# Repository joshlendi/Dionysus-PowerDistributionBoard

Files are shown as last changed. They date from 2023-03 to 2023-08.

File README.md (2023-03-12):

# Dionysus: Automated Indoor Hydroponic Garden

## Description
The NFT hydroponic garden will consist of four vertical rows with five plants each. The structure will contain all necessary systems to grow small plants. 
The control system will be a closed-loop model based design deployed to an Arduino Due. An optional nutrient control system will monitor and adjust plant nutrient levels during operation. 

## Table of Contents
* Installation
* Contributing
* Credits
* License

## Installation
1. Download [Dionysus-Power Distribution Board] and unzip
2. Open the KiCAD project folder. **Note**, some symbols' and footprints' may need correction. All symbols and footprints can be found in the *libraries* folder within the project.

## Contributing
* See [CONTRIBUTING.md](https://github.com/joshlendi/Dionysus-PowerDistributionBoard/blob/master/CONTRIBUTING) for more information

## Credits
* Include a section for credits in order to highlight and link to the authors of your project.

## License
* GNU General Public License v3.0
	* See [LICENSE.md](https://github.com/joshlendi/Dionysus-PowerDistributionBoard/blob/master/LICENSE) for more information

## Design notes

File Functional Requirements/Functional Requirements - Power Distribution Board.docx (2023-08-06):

# Dionysus Power Distribution Board

# Functional Requirements [XX/XX/XXXX]

Contents

# Overview

The overview section should include a brief description of the project and functionality so that someone outside of the project team would be able to understand the project. The section should include a list of commonly used acronyms and abbreviations, a list of system components and their purpose, and inputs and outputs as discussed on the I/O list deliverable.

## Description

The Dionysus project will be a self-sufficient NFT hydroponic garden capable of growing small vegetables and herbs. The controller for Dionysus will be an Arduino Due microcontroller embedded in the power distribution motherboard.

The purpose is to create a control board that can handle the inputs and outputs necessary to operate a Dionysus system. Today’s microcontrollers and single board computers are not capable of driving all the components required. Additional hardware and circuitry are required.

Rather than a larger collection of harnessing, piggyback boards, and modifications, a single power distribution board will be created to handle the necessary inputs, outputs, and communications.

## Scope

In Scope | Out of Scope
Self-contained computer power | Raspberry Pi Model 4 and Compute Module compatibility
GPIO for IO expansion | Voltage and current feedback measurements on input/outputs
Raspberry Pi or Arduino based microcontroller | True grow light drivers
E-stop circuitry
Ability to add an optional nutrient control system

## Acronyms and Abbreviations

Acronym | Meaning | Notes
NCS | Nutrient Control System | XXXXXXXXXXX
LED | Light-emitting Diode | XXXXXXXXXXX
TWI | Two-Wire Interface | Also known as I2C
TWD | Two-Wire Data | Also known as SDA
TWCK | Two-Wire Clock | Also known as SCL
CAN | Controller Area Network
USART | Universal Asynchronous Receive/Transmit
SPI | Serial Peripheral Interface
STB | Short to Battery
STG | Short to Ground

# System Components

Abbreviation | Meaning | Notes
XXXXX | XXXXXXXXX | XXXXXXXXXXXXXX

# Board Controller

The system controller will be an Arduino Due powered by a 32-bit ARM Cortex-M3 processor. The board contains 54 digital input/output pins, 12 analog inputs, and 2 digital-to-analog pins. For communication, it has 4 UART busses, 2 TWI, and a single SPI header. Refer to Arduino’s official website (https://store-usa.arduino.cc/products/arduino-due?selectedStore=us) for more information.

The Due board will be installed as a piggy back board using stacking header pins. This does require an Arduino Due without headers to be purchased and have stacked headers added. Power will be provided to the power input pin through these headers.

The Due board operates at 3.3V. Therefore, all logical inputs and outputs will be restricted to 3.3V, and communications are restricted to 3.3V logic levels.

Board Specifications

Microcontroller: AT91SAM3X8E

Operating Voltage: 3.3 VDC

Input Voltage: 6-16 VDC (7-12 VDC recommended)

Digital I/O Pins: 54

Analog Input Pins: 12

Analog Output Pins: 2

I/O Output Current Total: 130 mA

3.3V Power Pin Current: 800 mA

5V Power Pin Current: 800 mA

Flash Memory: 512 KB

SRAM: 96KB

Clock Speed: 84 Mhz

# Inputs

Name | Description
Ambient Temperature | Ambient temperature of environment
Ambient Light | Ambient light available to plants
Emergency Stop Feedback | Emergency stop feedback to control system
NCS Flow Rate | Volumetric flow rate going through nutrient control system
NCS Temperature In | Input temperature to nutrient control system
Chemical 1 Level Minimum | Chemical 1 tank almost empty. Signals operator to refill tank.
Chemical 2 Level Minimum | Chemical 2 tank almost empty. Signals operator to refill tank.
Chemical 3 Level Minimum | Chemical 3 tank almost empty. Signals operator to refill tank.
Chemical 4 Level Minimum | Chemical 4 tank almost empty. Signals operator to refill tank.
Chemical 5 Level Minimum | Chemical 5 tank almost empty. Signals operator to refill tank.
Chemical 1 Pump Feedback | Chemical 1 peristaltic pump dispensing active
Chemical 2 Pump Feedback | Chemical 2 peristaltic pump dispensing active
Chemical 3 Pump Feedback | Chemical 3 peristaltic pump dispensing active
Chemical 4 Pump Feedback | Chemical 4 peristaltic pump dispensing active
Chemical 5 Pump Feedback | Chemical 5 peristaltic pump dispensing active
Reservoir pH | Reservoir pH level measured in nutrient control system
Reservoir Flow Rate | Volumetric flow rate out of reservoir
Reservoir Temperature In | Input temperature to reservoir
Reservoir Temperature Out | Output temperature of reservoir
Reservoir TDS | Reservoir total dissolved solids measured in nutrient control system
Reservoir Level Minimum | Reservoir water level almost empty

## Input Processing

The input processing section should include a description of the input processing requirements of the system. This should cover details about Debounce, Anti Tie-down, Overrides, dead banding, and other project specific input processing options.

# Outputs

Name | Abbreviation | Description
LED Channel 1 | LEDCh1 | 3-wire RGB LED channel 1
LED Channel 2 | LEDCh2 | 3-wire RGB LED channel 2
LED Channel 3 | LEDCh3 | 3-wire RGB LED channel 3
LED Channel 4 | LEDCh4 | 3-wire RGB LED channel 4
LED Channel 5 | LEDCh5 | 3-wire RGB LED channel 5
LED Channel 6 | LEDCh6 | 3-wire RGB LED channel 6
LED Channel 7 | LEDCh7 | 3-wire RGB LED channel 7
LED Channel 8 | LEDCh8 | 3-wire RGB LED channel 8
NCS Pump Activation | NCSPmpAct | Nutrient control system water pump activation
Reservoir Heater Activation | RsvrHeaterAct | Reservoir heater activation
Reservoir Pump Activation | RsvrPmpAct | Reservoir water pump activation
Chemical 1 Pump | Chem1Pmp | Chemical 1 peristaltic dispensing control
Chemical 2 Pump | Chem2Pmp | Chemical 2 peristaltic dispensing control
Chemical 3 Pump | Chem3Pmp | Chemical 3 peristaltic dispensing control
Chemical 4 Pump | Chem4Pmp | Chemical 4 peristaltic dispensing control
Chemical 5 Pump | Chem5Pmp | Chemical 5 peristaltic dispensing control

## Output Processing

This section should be used if there are outputs to be processed by the control system.

# Power Management Controller

The Arduino Due board requires 7 VDC to 12 VDC. The water pump(s) and reservoir heater activation use a FET to provide medium to high power to AC relays. Flyback protection should be used. The chemical peristaltic pumps and grow lights operate between 12 and 24 volts.

Power regulation is required for the board. Power management will consist of voltage regulation for the board’s controller, sensors, and other low power accessories. Four high side drivers will be used to power larger loads, such as peristaltic pumps, grow lights, and water pump relay coil activation.

The board must have an input voltage of 12 to 24 volts DC. Circuit protections must be used to protect the board from reverse polarity, overvoltage, and overcurrent.

The board must output voltages at 3.3 VDC, 9 VDC, and input voltage ranges. Each power source shall be protected by circuit protection devices. Fuses should be used for each device powered and located as close to the source as possible.

[need to specify what devices are powered by which bus]

[insert the power management calculation tables here]

[Specify the current limits for each power rail]

# Subsystems

## Two-Wire Interface Bus Isolator

The Atlas Scientific EZO boards require voltage isolation if multiple boards are used on the same two-wire bus. Each EZO board will have a voltage and communication isolator circuit. It uses a two-wire interface digital isolator along with an isolated DC-DC converter.

The isolated busses require termination resistors.

## GPIO

10 digital input/outputs and 5 analog inputs are available as general purpose input/outputs. These are available to the end user for additional sensors and system input/outputs.

Digital input/outputs should be protected against short to battery and short to ground

Overvoltage protection, overcurrent protection, back EMF protection, current limiting, basic filtering, external clipping diodes

## Pulse Width Modulation Controller

The grow lights used will be 3-wire RGB LED lights requiring brightness and color control. An RGB PWM LED driver will be used to drive at least 2 channels of grow lights. Additional channels may be add if space and circuitry constraints allow. Red and blue will be the main colors used.

PWM control will be used to control the brightness of the LEDs. This simulates the rising and setting of the sun.

Optional feature would be a way to create sectors of addressable LEDs. This would allow for simulating the sun moving east to west in the sky.

## Real-time Clock

This optional feature would be nice to have for data logging and future product improvements.

## Temperature Sensor

For the first design iteration, digital 1-wire temperature sensors, Maxim DS18B20, are acceptable. They require no additional hardware or circuitry to integrate. The digital communication bus must be scanned on start up to search for all available sensors.

5 temperature sensor channels are available.

There is no requirement for PCBA temperature sensors. The circuit board should have at least 1 temperature sensor installed for board diagnostics and ambient redundancy.

## CAN Bus

The microcontroller has CAN bus communication available. A CAN bus transceiver will be implemented into the PDB. CAN high and low will be externally available to the end user for additional functionality.

CAN high, low, 12 volt power, and 12 volt ground will be available in a four pin terminal block.

The CAN bus has selectable termination using a selector switch.

## EZO Board

The motherboard will allow for at least 4 Atlas Scientific EZO sensor boards. They use 2-three pin headers in a daughterboard configuration. Any EZO board must be compatible in any of the four spots.

A BNC or three pin terminal block will be used to connect the EZO sensor to the power distribution board.

## Peristaltic Pump

The Atlas Scientific peristaltic pumps will be used. These require 12 to 24 volt power for the motor and 3.3 to 5 volt power for the control section. Motor power is supplied through a two pin terminal block on the PDB and pump. The control section uses a Molex connection.

The circuit board must accommodate at least 5 peristaltic pumps.

## Water Pump

The PDB must be able to drive 2 AC relays. These will activate the reservoir and nutrient control system pumps. Each pump output will have its own two position terminal block, a positive and negative.

## Water Heater

The PDB must be able to drive an AC relay that provides power to the reservoir heater.

## Air Pump

The PDB must be able to drive an AC relay that provides power to the reservoir air pump.

# Operating Mode

This section should define conditional operating modes of the system for expected use.

# Failure Modes

A failure mode is a mode that the system may enter into automatically upon a system fault. The most common system faults occur at an input or an output. This section should list potential input/output/communication faults and system responses.

# Communications

This section should describe the modes of communication used on the project, examples including CAN, Radio, Ethernet, Multiplex, etc.

The circuit board will be a flexible design for the end user. Some or all of the inputs, outputs, and sensors may be used. Internal communication must be flexible. A two-wire interface bus will be used for internal board communication. The EC, pH, flow meter, and peristaltic pumps specified for this project are TWI and UART compatible. UART is simpler in its design but does not allow for the flexibility that a TWI bus has.

All communication busses will have selectable termination resistors at various points to allow the end user to select where the bus is terminated.

An external connector will be provided for TWI communication to an external board should once be added.

# Limiting and Interlock

This section should describe the components/devices/functionality which will limit functionality or provide interlock signals for the device. This section should describe what components allow for expected functional use.

## Emergency Stop Device Interlock

The emergency stop device interlock consists of two circuits: a hardwired loop and feedback signal.

The feedback signal provides confirmation to the control system to prevent false errors.

The hardwired loop runs through various connectors to prevent power from being delivered to various components.

# Calibrations

This section should list the expected calibrated inputs to the system.

# Diagnostics

This section should list the planned diagnostic/health information that is intended.

## LED Indication

LED indication will be provided for all major functions of the board.

Indication Color | Function
Green | Device functioning properly
Yellow | Device functionality limited, but not crucial to operation
Red | Device error occurred. Functionality is disabled.
Blue
Orange/Amber

Indication Pattern | Function
Solid
Flashing
Flashing

Component | Component Signal | Color
Input Voltage | - | Green
3.3V Regulator | Regulator output | Green
5.0V Regulator | Regulator output | Green
High Side Drivers | Driver output | Green
Chemical Pumps | Pump interrupt | Green
NCS Pump | Pump FET activation | Green
Reservoir Pump | Pump FET activation | Green
Reservoir Heater | Heater FET activation | Green
TWI Busses | Data FET | Green
UART Bus | Data FET | Green
CAN Bus | Data FET | Green

# External Connect

Header pins are available for all communication busses.

# Telematics

This board does not contain any ability to transmit data.

# Data Logging

This board does not contain any ability to log data.

# Applicable Standards

This section should list the standard requirements for the project, as well as the expected use of standardized information, such as EPS, Library Blocks, IEEE, SAE, etc.

# Appendix

# Figures

# Tables

# Revision History

Revision History
When: | Who: | What:
XX/XX/XXXX | XXXXXXX | XXXXXXXXXXXXXXXXXXXXXXXXX

Functional Requirement

DocXXXXXXX XX/XX/XXXX

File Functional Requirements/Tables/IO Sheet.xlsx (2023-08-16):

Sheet: IO Statistics
 | Power | 12
 | Ground | 9
Inputs | Keyswitch | #REF!
 | Switch-to-Battery | #REF!
 | Switch-to-Ground | #REF!
 | Voltage-to-Digital | #REF!
Outputs | Switch-to-Battery | #REF!
 | Switch-to-Ground | #REF!
 | Pulse Width Modulation | #REF!
Communication | Two Wire Interface | #REF!

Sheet: IO Sheet
Signal Name | Description | Direction | Type | Point A |  |  | Point B
 |  |  |  | Device 1 | Device 1 Connector | Pin | Device 2 | Device 2 Connector | Pin
Vin | Input power | Power | PWR | Internal - PMC | - | - | Power | TB1 | 1
Ground |  | Power | GND | Internal - PMC | - | - | Power | TB1 | 2
Keyswitch |  | Input | KEYSW | Internal - PMC | - | - | System | TB2 | 1
EStopDevOut | Estop loop power - start of loop | Power | PWR | Internal - Sys | - | - | System | TB2 | 2
EStopDevIn | Estop loop - end of loop | Input | STB | Arduino Due | Controller header | D24 | System | TB2 | 3
EStopFdbk | Emergency stop feedback | Input | STB | Arduino Due | Controller header | D25 | System | TB2 | 4
CtrlReset | Microcontroller Reset | Input | STG | Arduino Due | Controller header | RESET | System | TB2 | 5
AmbLit | Ambient light sensor | Input | VTD | Arduino Due | Controller header | A9 | Sensor | TB3 | 1
RsvrLvlMin | Reservoir level minimum | Input | STB | Arduino Due | Controller header | D35 | Sensor | TB3 | 2
AmbTemp | Ambient temperature sensor | Comm | 1-Wire | Arduino Due | Controller header | D35 | Sensor | TB3 | 3
RsvrTempIn | Reservoir temperature in | Comm | 1-Wire | Arduino Due | Controller header | D35 | Sensor | TB3 | 4
RsvrTempOut | Reservoir temperature out | Comm | 1-Wire | Arduino Due | Controller header | D35 | Sensor | TB3 | 5
SpareTemp | Spare temperature sensor | Comm | 1-Wire | Arduino Due | Controller header | D35 | Sensor | TB3 | 6
AmbEnv - TWCK | Ambient environment sensor | Comm | TWCK | Arduino Due | Controller header | SCL | Sensor | TB3 | 7
AmbEnv - TWD | Ambient environment sensor | Comm | TWD | Arduino Due | Controller header | SDA | Sensor | TB3 | 8
AccPwr1 | 3.3V accessory power | Power | PWR | Internal - PMC | - | - | Sensor | TB3 | 9
Ground |  | Power | GND | Internal - PMC | - | - | Sensor | TB3 | 10
MainPwr1 | Reservoir pump power | Power | PWR | Internal - PMC | - | - | Reservoir Pump | TB4 | 1
Ground |  | Power | GND | Internal - PMC | - | - | Reservoir Pump | TB4 | 2
MainPwr2 | Reservoir heater power | Power | PWR | Internal - PMC | - | - | Reservoir Heater | TB5 | 1
Ground |  | Power | GND | Internal - PMC | - | - | Reservoir Heater | TB5 | 2
Nutr1LvlMin | Nutrient 1 Level Minimum | Input | STB | Arduino Due | Controller header | D44 | NCS | TB6 | 1
Nutr1PerPmpInt | Nutrient 1 Peristalic Pump Interrupt | Input | STB | Arduino Due | Controller header | D45 | NCS | TB6 | 2
Nutr2LvlMin | Nutrient 2 Level Minimum | Input | STB | Arduino Due | Controller header | D46 | NCS | TB6 | 3
Nutr2PerPmpInt | Nutrient 2 Peristalic Pump Interrupt | Input | STB | Arduino Due | Controller header | D47 | NCS | TB6 | 4
Nutr3LvlMin | Nutrient 3 Level Minimum | Input | STB | Arduino Due | Controller header | D48 | NCS | TB6 | 5
Nutr3PerPmpInt | Nutrient 3 Peristalic Pump Interrupt | Input | STB | Arduino Due | Controller header | D49 | NCS | TB6 | 6
PhDecrLvlMin | pH Decrease Level Minimum | Input | STB | Arduino Due | Controller header | D50 | NCS | TB6 | 7
PhDecrPerPmpInt | pH Decrease Peristalic Pump Interrupt | Input | STB | Arduino Due | Controller header | D51 | NCS | TB6 | 8
PhIncrLvlMin | pH Increase Level Minimum | Input | STB | Arduino Due | Controller header | D52 | NCS | TB6 | 9
PhIncrPerPmpInt | pH Increase Peristalic Pump Interrupt | Input | STB | Arduino Due | Controller header | D53 | NCS | TB6 | 10
NCSTempIn | Nutrient Control System Temperature In | Comm | 1-Wire | Arduino Due | Controller header | D35 | NCS | TB6 | 11
NCS - TWCK | Nutrient Control System TWI bus | Comm | TWCK | Arduino Due | Controller header | SCL | NCS | TB6 | 12
NCS - TWD | Nutrient Control System TWI bus | Comm | TWD | Arduino Due | Controller header | SDA | NCS | TB6 | 13
AccPwr3 | 3.3V accessory power | Power | PWR | Internal - PMC | - | - | NCS | TB6 | 14
Ground |  | Power | GND | Internal - PMC | - | - | NCS | TB6 | 15
MainPwr4 | NCS pump power | Power | PWR | Internal - PMC | - | - | NCS Pump | TB7 | 1
Ground |  | Power | GND | Internal - PMC | - | - | NCS Pump | TB7 | 2
D1 | General purpose input/output pins |  |  | Arduino Due | Controller header | D2 | GPIO - Digital | TB8 | 1
D2 | General purpose input/output pins |  |  | Arduino Due | Controller header | D3 | GPIO - Digital | TB8 | 2
D3 | General purpose input/output pins |  |  | Arduino Due | Controller header | D4 | GPIO - Digital | TB8 | 3
D4 | General purpose input/output pins |  |  | Arduino Due | Controller header | D5 | GPIO - Digital | TB8 | 4
D5 | General purpose input/output pins |  |  | Arduino Due | Controller header | D6 | GPIO - Digital | TB8 | 5
D6 | General purpose input/output pins |  |  | Arduino Due | Controller header | D7 | GPIO - Digital | TB8 | 6
D7 | General purpose input/output pins |  |  | Arduino Due | Controller header | D8 | GPIO - Digital | TB8 | 7
D8 | General purpose input/output pins |  |  | Arduino Due | Controller header | D9 | GPIO - Digital | TB8 | 8
D9 | General purpose input/output pins |  |  | Arduino Due | Controller header | D10 | GPIO - Digital | TB8 | 9
D10 | General purpose input/output pins |  |  | Arduino Due | Controller header | D11 | GPIO - Digital | TB8 | 10
AccPwr2 | 3.3V accessory power | Power | PWR | Internal - PMC | - | - | GPIO - Digital | TB8 | 11
Ground |  | Power | GND | Internal - PMC | - | - | GPIO - Digital | TB8 | 12
A1 | General purpose analog input pins | Input | VTD | Arduino Due | Controller header | A0 | GPIO - Analog | TB9 | 1
A2 | General purpose analog input pins | Input | VTD | Arduino Due | Controller header | A1 | GPIO - Analog | TB9 | 2
A3 | General purpose analog input pins | Input | VTD | Arduino Due | Controller header | A2 | GPIO - Analog | TB9 | 3
A4 | General purpose analog input pins | Input | VTD | Arduino Due | Controller header | A3 | GPIO - Analog | TB9 | 4
A5 | General purpose analog input pins | Input | VTD | Arduino Due | Controller header | A4 | GPIO - Analog | TB9 | 5
DAC1 | General purpose analog output pins | Output | VTD | Arduino Due | Controller header | DAC1 | GPIO - Analog | TB9 | 6
DAC2 | General purpose analog output pins | Output | VTD | Arduino Due | Controller header | DAC2 | GPIO - Analog | TB9 | 7
AccPwr2 | 3.3V accessory power | Power | PWR | Internal - PMC | - | - | GPIO - Analog | TB9 | 8
Ground |  | Power | GND | Internal - PMC | - | - | GPIO - Analog | TB9 | 9
TWCK0 | Two-wire interface bus 1 | Comm | TWCK | Arduino Due | Controller header | D21/SCL | GPIO - Comm | TB10 | 1
TWD0 | Two-wire interface bus 1 | Comm | TWD | Arduino Due | Controller header | D20/SDA | GPIO - Comm | TB10 | 2
TWCK1 | Two-wire interface bus 2 | Comm | TWCK | Arduino Due | Controller header | SCL1 | GPIO - Comm | TB10 | 3
TWD1 | Two-wire interface bus 2 | Comm | TWD | Arduino Due | Controller header | SDA1 | GPIO - Comm | TB10 | 4
RXD | USART bus receive | Comm | USART | Arduino Due | Controller header | D0/RX0 | GPIO - Comm | TB10 | 5
TXD | USART bus transmit | Comm | USART | Arduino Due | Controller header | D1/TX0 | GPIO - Comm | TB10 | 6
CAN-H | CAN bus 1 | Comm | CAN-H | Internal - GPIO | - | - | GPIO - Comm | TB10 | 7
CAN-L | CAN bus 1 | Comm | CAN-L | Internal - GPIO | - | - | GPIO - Comm | TB10 | 8
1-Wire | 1-Wire header | Comm | 1-Wire | Arduino Due | Controller header | D35 | GPIO - Comm | TB10 | 9
AccPwr2 | 3.3V accessory power | Power | PWR | Internal - PMC | - | - | GPIO - Comm | TB10 | 10
Ground |  | Power | GND | Internal - PMC | - | - | GPIO - Comm | TB10 | 11
LEDCh1-R | LED Channel 1 - Red | Output | PWM | Internal - LED Ctrl | - | - | LED Ch1 | TB11 | 1
LEDCh1-G | LED Channel 1 - Green | Output | PWM | Internal - LED Ctrl | - | - | LED Ch1 | TB11 | 2
LEDCh1-B | LED Channel 1 - Blue | Output | PWM | Internal - LED Ctrl | - | - | LED Ch1 | TB11 | 3
LEDCh2-R | LED Channel 2 - Red | Output | PWM | Internal - LED Ctrl | - | - | LED Ch2 | TB12 | 1
LEDCh2-G | LED Channel 2 - Green | Output | PWM | Internal - LED Ctrl | - | - | LED Ch2 | TB12 | 2
LEDCh2-B | LED Channel 2 - Blue | Output | PWM | Internal - LED Ctrl | - | - | LED Ch2 | TB12 | 3
LEDCh3 - R | LED Channel 3 - Red | Output | PWM | Internal - LED Ctrl | - | - | LED Ch3 | TB13 | 1
LEDCh3 - G | LED Channel 3 - Green | Output | PWM | Internal - LED Ctrl | - | - | LED Ch3 | TB13 | 2
LEDCh3 - B | LED Channel 3 - Blue | Output | PWM | Internal - LED Ctrl | - | - | LED Ch3 | TB13 | 3
LEDCh4 -R | LED Channel 4 -Red | Output | PWM | Internal - LED Ctrl | - | - | LED Ch4 | TB14 | 1
LEDCh4 -G | LED Channel 4 -Green | Output | PWM | Internal - LED Ctrl | - | - | LED Ch4 | TB14 | 2
LEDCh4 -B | LED Channel 4 -Blue | Output | PWM | Internal - LED Ctrl | - | - | LED Ch4 | TB14 | 3
LEDCh5 -R | LED Channel 5 -Red | Output | PWM | Internal - LED Ctrl | - | - | LED Ch5 | TB15 | 1
LEDCh5 -G | LED Channel 5 -Green | Output | PWM | Internal - LED Ctrl | - | - | LED Ch5 | TB15 | 2
LEDCh5 -B | LED Channel 5 -Blue | Output | PWM | Internal - LED Ctrl | - | - | LED Ch5 | TB15 | 3
LEDCh6 -R | LED Channel 6 -Red | Output | PWM | Internal - LED Ctrl | - | - | LED Ch6 | TB16 | 1
LEDCh6 -G | LED Channel 6 -Green | Output | PWM | Internal - LED Ctrl | - | - | LED Ch6 | TB16 | 2
LEDCh6 -B | LED Channel 6 -Blue | Output | PWM | Internal - LED Ctrl | - | - | LED Ch6 | TB16 | 3
LEDCh7 - R | LED Channel 7 - Red | Output | PWM | Internal - LED Ctrl | - | - | LED Ch7 | TB17 | 1
LEDCh7 - G | LED Channel 7 - Green | Output | PWM | Internal - LED Ctrl | - | - | LED Ch7 | TB17 | 2
LEDCh7 - B | LED Channel 7 - Blue | Output | PWM | Internal - LED Ctrl | - | - | LED Ch7 | TB17 | 3
LEDCh8 - R | LED Channel 8 - Red | Output | PWM | Internal - LED Ctrl | - | - | LED Ch8 | TB18 | 1
LEDCh8 - G | LED Channel 8 - Green | Output | PWM | Internal - LED Ctrl | - | - | LED Ch8 | TB18 | 2
LEDCh8 - B | LED Channel 8 - Blue | Output | PWM | Internal - LED Ctrl | - | - | LED Ch8 | TB18 | 3
CtrlPwr | 9V controller power | Power | PWR | Internal - PMC | - | - | Arduino Due | Controller header | VIN
MainPwr3 | Grow light power | Power | PWR | Internal - PMC | - | - | Internal - LED Ctrl | - | -
TWCK | LED Driver 1 TWI Bus | Comm | TWCK | Arduino Due | Controller header
TWD | LED Driver 1 TWI Bus | Comm | TWD | Arduino Due | Controller header
TWCK | LED Driver 2 TWI Bus | Comm | TWCK | Arduino Due | Controller header
TWD | LED Driver 2 TWI Bus | Comm | TWD | Arduino Due | Controller header
NCSPmpAct | Nutrient Control System Pump Activation | Output | STB | Arduino Due | Controller header | D42
NCSPmpActFdbk | Nutrient Control System Pump Activation Feedback | Input | STB | Arduino Due | Controller header | D43
AccPwrAct | Accessory power activation | Output | STB | Arduino Due | Controller header | D22
MainPwrAct | Main power activation | Output | STB | Arduino Due | Controller header | D23
MainPwr1Fdbk | Main power 1 measured feedback current | Input | VTD | Arduino Due | Controller header | A5
MainPwr2Fdbk | Main power 2 measured feedback current | Input | VTD | Arduino Due | Controller header | A6
MainPwr3Fdbk | Main power 3 measured feedback current | Input | VTD | Arduino Due | Controller header | A7
MainPwr4Fdbk | Main power 4 measured feedback current | Input | VTD | Arduino Due | Controller header | A8
RsvrPmpAct | Reservoir pump activation | Output | STB | Arduino Due | Controller header | D26
RsvrPmpActFdbk | Reservoir pump activation feedback | Input | STB | Arduino Due | Controller header | D27
RsvrHeaterAct | Reservoir heater activation | Output | STB | Arduino Due | Controller header | D28
RsvrHeaterActFdbk | Reservoir heater activation feedback | Input | STB | Arduino Due | Controller header | D29
CANRX | CAN bus | Comm | CAN | Arduino Due | Controller header | CANRX | Internal - GPIO
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

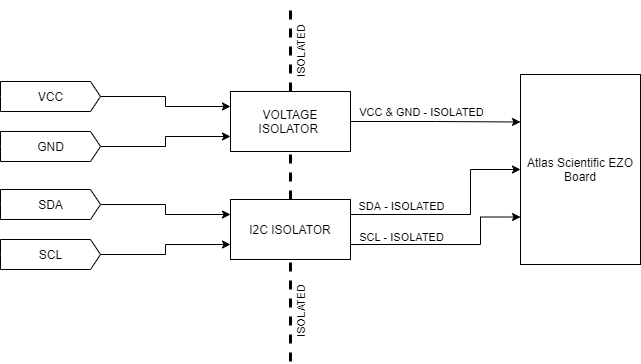
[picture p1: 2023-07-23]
Functional Requirements/Figures/Functional Requirements - Power Distribution Board_Diagrams-I2C Bus Isolator.png

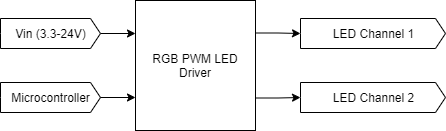
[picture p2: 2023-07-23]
Functional Requirements/Figures/Functional Requirements - Power Distribution Board_Diagrams-PWM.png

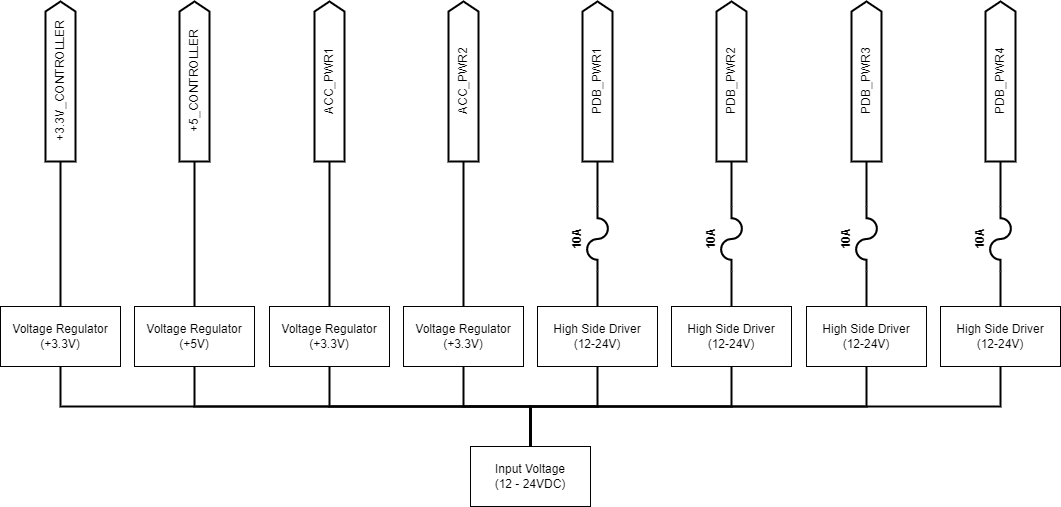
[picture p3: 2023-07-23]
Functional Requirements/Figures/Functional Requirements - Power Distribution Board_Diagrams-Power Management.png

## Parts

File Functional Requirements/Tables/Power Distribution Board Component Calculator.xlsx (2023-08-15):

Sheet: Total Power Requirements
 | Input Voltage [V] | Input Current [A] | Input Power [W] | Efficiency [%] | Output Voltage [V] | Current [A] | Power [W]
Accessory Power 1 | 12.00 | 1.16 | 13.89 | 95% | 3.30 | 4.00 | 13.20
Accessory Power 2 | 12.00 | 0.18 | 2.11 | 95% | 3.30 | 0.61 | 2.00
Accessory Power 3 | 12.00 | 0.39 | 4.71 | 95% | 3.30 | 1.35 | 4.47
Controller Power 1 | 12.00 | 0.79 | 9.47 | 95% | 9.00 | 1.00 | 9.00
Main Power 1 | 12.00 | 1.05 | 12.63 | 95% | 12.00 | 1.00 | 12.00
Main Power 2 | 12.00 | 1.05 | 12.63 | 95% | 12.00 | 1.00 | 12.00
Main Power 3 | 12.00 | 1.05 | 12.63 | 95% | 12.00 | 1.00 | 12.00
Main Power 4 | 12.00 | 2.11 | 25.26 | 95% | 12.00 | 2.00 | 24.00
Total | 12.00 | 7.78 | 93.34
Table #: Total Bus Power Requirements
 | Input Voltage [V] | Input Current [A] | Input Power [W] | Efficiency [%] | Output Voltage [V] | Current [A] | Power [W]
Accessory Power 1 | 12.00 | 0.00 | 0.00 | 95% | 3.30 |  | 0.00
Accessory Power 2 | 12.00 | 0.00 | 0.00 | 95% | 3.30 |  | 0.00
Accessory Power 3 | 12.00 | 0.00 | 0.00 | 95% | 3.30 |  | 0.00
Controller Power 1 | 12.00 | 0.00 | 0.00 | 95% | 9.00 |  | 0.00
Main Power 1 | 12.00 | 0.00 | 0.00 | 95% | 12.00 |  | 0.00
Main Power 2 | 12.00 | 0.00 | 0.00 | 95% | 12.00 |  | 0.00
Main Power 3 | 12.00 | 0.00 | 0.00 | 95% | 12.00 |  | 0.00
Main Power 4 | 12.00 | 0.00 | 0.00 | 95% | 12.00 |  | 0.00
Total | 12.00 | 0.00 | 0.00
Table #: Bus Power Limits

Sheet: Accessory Power Bus - 3.3V
Device | Qty | Voltage [V] | Current [A] | Power [W] | Total Current [A] | Total Power [W]
GPIO Header | 15 | 3.30 | 0.20 | 0.66 | 3.00 | 9.90
Communication Headers | 5 | 3.30 | 0.20 | 0.66 | 1.00 | 3.30
 |  |  |  |  | 4.00 | 13.20
Table #: Accessory Power 2 - 3.3V Devices
Device | Qty | Voltage [V] | Current [A] | Power [W] | Total Current [A] | Total Power [W]
Liquid Level Switch | 3 | 3.30 | 0.0025 | 0.01 | 0.01 | 0.02
Temperature Sensor | 5 | 3.30 | 0.10 | 0.33 | 0.50 | 1.65
Ambient Environment Sensor | 1 | 3.30 | 0.10 | 0.33 | 0.10 | 0.33
 |  |  |  |  | 0.61 | 2.00
Table #: Accessory Power 1 - 3.3V Devices
Device | Qty | Voltage [V] | Current [A] | Power [W] | Total Current [A] | Total Power [W]
Peristaltic Pump Logic | 5 | 3.30 | 0.01 | 0.04 | 0.06 | 0.21
Liquid Level Switch | 5 | 3.30 | 0.0025 | 0.01 | 0.01 | 0.04
Isolated DC-DC converter | 4 | 3.30 | 0.20 | 0.66 | 0.80 | 2.64
Digital TWI Isolator | 4 | 3.30 | 0.12 | 0.40 | 0.48 | 1.58
 |  |  |  | 0.00 | 0.00 | 0.00
 |  |  |  |  | 1.29 | 4.27
Table #: Accessory Power 3 - 3.3V Devices
Device | Qty | Voltage [V] | Current [A] | Power [W] | Total Current [A] | Total Power [W]
Accessory Power 1 |  | 3.30 | 0.0025 | 0.01 | 0.01 | 0.02
Accessory Power 2 |  | 3.30 | 0.10 | 0.33 | 0.50 | 1.65
Accessory Power 3 |  | 3.30 | 0.10 | 0.33 | 0.10 | 0.33
 |  |  |  |  | 0.61 | 2.00
Table #: Accessory Power Bus - 3.3V Total

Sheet: Controller Power Bus - 9V
Device | Qty | Voltage [V] | Current [A] | Power [W] | Total Current [A] | Total Power [W]
Arduino Due Controller | 1 | 9.00 | 1.00 | 9.00 | 1.00 | 9.00
 |  |  |  |  | 1.00 | 9.00
Table #:
Device | Qty | Voltage [V] | Current [A] | Power [W] | Total Current [A] | Total Power [W]
 |  |  |  |  | 0.00 | 0.00
Table #:
Device | Qty | Voltage [V] | Current [A] | Power [W] | Total Current [A] | Total Power [W]
 |  |  |  |  | 0.00 | 0.00
Table #:

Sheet: Main Power Bus - Vin
Device | Qty | Voltage [V] | Current [A] | Power [W] | Total Current [A] | Total Power [W]
Reservoir Pump Activation | 1 | 12.00 | 1.00 | 12.00 | 1.00 | 12.00
 |  |  |  |  | 1.00 | 12.00
Table #: Main Power 1 - Vin Devices
Device | Qty | Voltage [V] | Current [A] | Power [W] | Total Current [A] | Total Power [W]
Reservoir Heater Activation | 1 | 12.00 | 1.00 | 12.00 | 1.00 | 12.00
 |  |  |  |  | 1.00 | 12.00
Table #: Main Power 2 - Vin Devices
Device | Qty | Voltage [V] | Current [A] | Power [W] | Total Current [A] | Total Power [W]
Grow Lights | 1 | 12.00 | 1.00 | 12.00 | 1.00 | 12.00
 |  |  |  |  | 1.00 | 12.00
Table #: Main Power 3 - Vin Devices
Device | Qty | Voltage [V] | Current [A] | Power [W] | Total Current [A] | Total Power [W]
Peristaltic Pump Power | 5 | 12.00 | 0.40 | 4.80 | 2.00 | 24.00
 |  |  |  |  | 2.00 | 24.00
Table #: Main Power 4 - Vin Devices

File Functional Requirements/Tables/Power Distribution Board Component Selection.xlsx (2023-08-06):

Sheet: Sheet1
Terminal block | Power (12-24VDC)
 | Signal (0-5V)
Resistors | 4.7k
 | 1M
 | LED resistor
 | Gate driver
Capacitors | Decoupling (10uF-0.1uF + 100pF)
LED | Red
 | Green
 | Blue
 | White
 | RGB?
Headers | 2 pin male (Jumper
 | 4 pin male (I2C diagnostic)
 | 3 pin female (EZO board)
Power MOSFET | N-channel (Grow lights)
MOSFET | N-channel (LED indicator)
 | P-channel (I2C indicator)
Voltage regulator | +3.3VDC (Calculate power)
 | +5VDC (Calculate power)
Fuses | Source voltages (3, 5, 12)
 | Peristalic pumps (pump pwr)
 | LED power
Polyfuse | Source voltages (3, 5, 12)
 | I/Os
TVS diode | Power supply
 | Pi power supply
 | Peristalic pumps (logic pwr)

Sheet: Terminal Block (2)
Component Filter Parameters
Number of Levels | Positions Per Level | Pitch | Mating Orientation | Current | Voltage | Wire Gauge | Mounting Type | Wire Termination | Features | Color
1 | 2 through 10 |  | Horizontal with Board | 15 to 60 | >24 |  | Through Hole | Screwless or Screw
 |  |  | Vertical with Board
 | Designator | Name | Description | Device | Positions | Voltage [V] | Current [A]
 |  | VIN |  |  | 2 | 24 | 55
 |  | LED CH1 |  |  | 3 | 17 | 0.72 |  |  |  | https://www.digikey.com/en/products/filter/terminal-blocks-wire-to-board/371
 |  | LED CH2 |  |  | 3 | 17 | 0.72 |  |  |  | https://www.digikey.com/en/products/detail/wago-corporation/2604-3102/15528152
 |  | LED CH3 |  |  | 3 | 17 | 0.72 |  |  |  | https://www.digikey.com/en/products/detail/phoenix-contact/1715022/260626
 |  | LED CH4 |  |  | 3 | 17 | 0.72 |  |  |  | https://www.digikey.com/en/products/detail/phoenix-contact/1929517/638167
 |  | LED CH5 |  |  | 3 | 17 | 0.72
 |  | LED CH6 |  |  | 3 | 17 | 0.72
 |  | LED CH7 |  |  | 3 | 17 | 0.72
 |  | LED CH8 |  |  | 3 | 17 | 0.72
 |  | PER PUMP 1 PWR |  |  | 2 | 24 | 0.4
 |  | PER PUMP 2 PWR |  |  | 2 | 24 | 0.4
 |  | PER PUMP 3 PWR |  |  | 2 | 24 | 0.4
 |  | PER PUMP 4 PWR |  |  | 2 | 24 | 0.4
 |  | PER PUMP 5 PWR |  |  | 2 | 24 | 0.4
 |  | NCS PUMP |  |  | 2 | 32 | 0.02
 |  | CHEM 1 LEVEL MIN |  |  | 3 | 16 | 0.025
 |  | CHEM 2 LEVEL MIN |  |  | 3 | 16 | 0.025
 |  | CHEM 3 LEVEL MIN |  |  | 3 | 16 | 0.025
 |  | CHEM 4 LEVEL MIN |  |  | 3 | 16 | 0.025
 |  | CHEM 5 LEVEL MIN |  |  | 3 | 16 | 0.025
 |  | RESERVOIR PUMP |  |  | 2 | 32 | 0.02
 |  | RESERVOIR HEATER |  |  | 2 | 32 | 0.02
 |  | AMBIENT LIGHT SENSOR |  |  | 2 | 12 | 0.02
 |  | E-STOP |  |  | 2 | 24 | 0.05
 |  | RSVR LVL MAX |  |  | 3 | 16 | 0.025
 |  | RSVR LVL MED |  |  | 3 | 16 | 0.025
 |  | RSVR LVL MIN |  |  | 3 | 16 | 0.025
 |  | AMB ENVIRONMENT |  |  | 4 | 5 | 0.02
 |  | TEMP SENSOR 1 |  |  | 3 | 5 | 0.05
 |  | TEMP SENSOR 2 |  |  | 3 | 5 | 0.05
 |  | TEMP SENSOR 3 |  |  | 3 | 5 | 0.05
 |  | TEMP SENSOR 4 |  |  | 3 | 5 | 0.05
 |  | TEMP SENSOR 5 |  |  | 3 | 5 | 0.05
 |  | EZO SENSOR 1 |  |  | 3 | 5 | 0.02
 |  | EZO SENSOR 2 |  |  | 3 | 5 | 0.02
 |  | EZO SENSOR 3 |  |  | 3 | 5 | 0.02
 |  | EZO SENSOR 4 |  |  | 3 | 5 | 0.02
 |  | GPIO (DIGITAL) |  |  | 12 | 3 | 3
 |  | GPIO (ANALOG) |  |  | 7 | 3 | 3
 |  | TWI-1 |  |  | 4 | 3 | 0.2
 |  | TWI-2 |  |  | 4 | 3 | 0.2
 |  | USART |  |  | 4 | 3 | 0.2
 |  | CAN |  |  | 4 | 3 | 0.2
 |  | 1-WIRE |  |  | 3 | 3 | 0.2

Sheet: Terminal Block
Part Number | Manufacturer | Manufacturer Part Number | Description | Voltage Rating (V) | Current Rating (A) | Connection Method | Positions | Cost | Purpose
277-5823-ND | Phoenix Contact | 1733415 | TERMINAL BLOCK, 2 POSITION, 35DEG, 5MM, PCB | 300 | 15 | Screw | 2 | $1.41 | Power and Ground
277-6326-ND | Phoenix Contact | 1733444 | TERMINAL BLOCK, 5 POSITION, 35DEG, 5MM, PCB | 300 | 15 | Screw | 5 | $1.41 | Signals
277-5872-ND | Phoenix Contact | 1733428 | TERMINAL BLOCK, 3 POSITION, 35DEG, 5MM, PCB | 300 | 15 | Screw | 3 | $1.41 | Signals
651-1700053 | Phoenix Contact | 1700053 | TERMINAL BLOCK, 1 POSITION, RIGHT ANGLE, 5MM, PCB | 250 | 24 | Screw | Stackable | $20.50 | Power and Ground
277-16662-ND | Phoenix Contact | 1929517 | TERMINAL BLOCK, 2 POSITION, HORIZONTAL, 10.16MM, PCB | 600 | 60 | Screw | 2 | $11.08 | Power and Ground
277-7663-ND | Phoenix Contact | 1990850 | TERMINAL BLOCK, 2 POSITION, HORIZONTAL, 3.5MM, PCB | 300 | 10 | Screwless | Multiple | $1.23 | Signals
277-14046-ND | Phoenix Contact | 1789618 | TERMINAL BLOCK, 2 POSITION, HORIZONTAL, 2.54MM, PCB | 150 | 6 | Screwless | Multiple | $2.59 | Signals

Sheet: LED
Part Number | Manufacturer | Manufacturer Part Number | Description | Color | QTY | Purpose
C503B-GAN-CB0F0791-ND | Cree Inc. | C503B-GAN-CB0F0791 | LED, GRN, 3.2V, 20mA, 5MM, THROUGH HOLE | Green | 1 | 12-24V Power and GND
C503B-GAN-CB0F0791-ND | Cree Inc. | C503B-GAN-CB0F0791 | LED, GRN, 3.2V, 20mA, 5MM, THROUGH HOLE | Green | 1 | 3.3-5V Power and GND
 |  |  |  |  | 5 | Peristalic Pumps
 |  |  |  | Red | 5 | Nutrient Tank Feedback
 |  |  |  | Green | 3 | EZO Board Power

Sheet: Misc. Functions
Part Number | Manufacturer | Manufacturer Part Number | Description | QTY

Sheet: Alternative Parts List
Part Number | Manufacturer | Manufacturer Part Number | Description | QTY
SI2302CDS-T1-E3CT-ND | Vishay Siliconix | SI2302CDS-T1-E3 | MOSFET, N-CH, 20V, 710mW, TO-236-3
CKC5106-ND | C&K | L101011MS02Q | SWITCH, ON-OFF, SPST, 28VDC/125VAC, 4ADC/ADC, SLIDE

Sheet: Power Consumption
 | Voltage (V) |  | Current (mA) |  |  | Power |  |  | Max Draw |  | Max Power (W)
Component | Min | Max | Min/Sleep | Nominal/Standby | Max | Min | Max | 3.3-5V Bus | 231.8 | mA | 1.159
EZO-PH | 3.3 | 5 | 1.16 | 16 | 18.3 |  | 91.5 | 12-24V Bus | 2000 | mA | 24
EZO-EC | 3.3 | 5 | 0.7 | 18.14 | 50 |  | 250
EZO_FLOW | 3.3 | 5 | 0.3 | 20.5 | 21 |  | 105
I2C Isolator | 3.3 | 5 |  | 20 | 20 |  | 66
Peristalic pump (logic) | 3.3 | 5 | 0.415 | 13.4 | 13.7 |  | 68.5 |  |  | Operating Voltage
Peristalic pump (motor) | 12 | 24 | 200 |  | 400 |  | 4800 |  | Companion Board | 3.3V | 5V
Nutrient tank min feedback | 4.5 | 15.4 |  |  | 2.5 |  | 11.25 | EZO Isolator | None | 20 | 15
Temperature sensor | 3.3 | 5 |  |  | 1.5 |  | 4.95 |  | EZO PH | 87 | 57 | 1481.8
 |  |  |  |  |  |  |  |  | EZO ORP | 84 | 58
 |  |  |  |  |  |  |  |  | EZO OXY | 84 | 53
 |  |  |  |  |  |  |  |  | EZO EC | 97 | 82
 |  |  |  |  |  |  |  |  | EZO RTD | 87 | 59

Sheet: Sheet 1
Part Number | Manufacturer | Manufacturer Part Number | Description | QTY | 12-24V power and gnd terminal block
277-5872-ND | Phoenix Contact | 1733428 | TERMINAL BLOCK, 3 POSITION, 35DEG, 5MM, PCB | 5 | 3.3-5V power and gnd terminal block
CC2108-ND | Sensata-Crydom | CL240D10R | RELAY, SOLID-STATE, SPST-NO, 3-32VDC INPUT, 24-280VAC OUTPUT, 10A | 2 | I2C terminal block
277-5823-ND | Phoenix Contact | 1733415 | TERMINAL BLOCK, 2 POSITION, 35DEG, 5MM, PCB | 2 | I2C termination jumpers
 |  |  | Current limiting resistor/diode | 2 | Peristalic pump terminal block
 |  |  | Voltage divider resistor | 3 | Nutrient tank min feedback terminal block
 |  |  |  |  | Temperature sensor terminal block
 |  |  |  |  | EZO boards
 |  |  |  |  | Male SMA probe connectors
 |  |  |  |  | Feedback LEDs
 |  |  |  |  | Switches
 |  |  |  |  | Fuses
 |  |  |  |  | I2C enable terminal block
 |  |  |  |  | Flow meter terminal block
 |  |  |  |  | Peristalic pump control harness pin header
Part Number | Manufacturer | Manufacturer Part Number | Description | QTY
277-5823-ND | Phoenix Contact | 1733415 | TERMINAL BLOCK, 2 POSITION, 35DEG, 5MM, PCB | 8
277-5872-ND | Phoenix Contact | 1733428 | TERMINAL BLOCK, 3 POSITION, 35DEG, 5MM, PCB | 2 | Additional flow meter and board
277-6326-ND | Phoenix Contact | 1733444 | TERMINAL BLOCK, 5 POSITION, 35DEG, 5MM, PCB | 1 | Reservoir level sensor
343-CONSMA001-C-G-ND | Linx Technologies Inc. | CONSMA001-C-G | CONNECTOR, SMA, RECEPTACLE,FEMALE, THROUGH HOLE, STRAIGHT | 3 | Temp_in sensor | 3 pos
 |  |  | I2C termination jumpers | 2 | Temp_out sensor | 3 pos
 |  |  | EZO board header pins | 8 | AC relay trigger | 2 pos
CKN11876-ND | C&K | L201011MS02Q | SWITCH, ON-OFF, DPST, 28VDC/125VAC, 4ADC/ADC, SLIDE | 1 | AC relay trigger | 2 pos
 |  |  | Source fuses | 2
WM4114-ND | Molex | 22272051 | CONNECTOR, HEADER, VERTICAL, 5 POSITION, THROUGH HOLE | 5 | LED power out
C503B-GAN-CB0F0791-ND | Cree Inc. | C503B-GAN-CB0F0791 | LED, GRN, 3.2V, 20mA, 5MM, THROUGH HOLE | 2 | ambient light sensor | 2 pos
 |  |  | SMA and TB switch | 1 | BME280
 |  |  | 5V regulator for pi power input | 1
 |  |  | 3V regulator for 3V components | 1
Part Number | Manufacturer | Manufacturer Part Number | Description | QTY
S4.7KCACT-ND | Stackpole Electronics Inc. | RNMF14FTC4K70 | RESISTOR, 4.7K, 0.25W, +-1%, AXIAL | 4
RNF18FTD1M00CT-ND | Stackpole Electronics Inc. | RNF18FTD1M00 | RESISTOR, 1M, 1/8W,1%, AXIAL | 2
493-12698-1-ND | Nichicon | UVP1H100MED1TD | CAPACITOR, 10uF, 50V, 20%, ALUMINUM, RADIAL | 6
584-ADM3260ARSZ | Analog Devices | ADM3260ARSZ | DIGITAL ISOLATOR, I2C, 2 CHANNEL, BIDIRECTIONAL, 3.3-5V, 2.5W | 1
IXFP16N50P-ND | IXYS | IXFP16N50P | MOSFET, N-CH, 500V, 300W, TO-220 | 1
S1.5KCACT-ND | Stackpole Electronics Inc. | RNMF14FTC1K504 | RESISTOR, 1.5K, 1/4W, 1%, AXIAL | 3

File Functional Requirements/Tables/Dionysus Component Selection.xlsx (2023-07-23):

Part Number | Supplier | Supplier Part Number | Manufacturer | Manufacturer Part Number | Capacity (gallons) | Capacity (liters) | Dimensions | Weight (lbs) | Lid | Material | Cost | Link
 | Plastic-mart | A-SP0006-5N | Ace Roto-Mold / Den-Hartog | SP0006-5N | 6 | 22.7125 | 15"L x 12"W x 8"H | 6 | 5" screw-on | Polyethylene | $41.99 | https://www.plastic-mart.com/product/2463/6-gallon-rectangle-flat-bottom-tank-sp0006-5n
 | Plastic-mart | A-SP0005-RT | Ace Roto-Mold / Den-Hartog | SP0005-RT | 5 | 22.7125 | 22"L x 10"W x 8"H | 6 | 5" screw-on | Polyethylene | $38.99 | https://www.plastic-mart.com/product/2465/5-gallon-rectangle-flat-bottom-tank-sp0005-rt

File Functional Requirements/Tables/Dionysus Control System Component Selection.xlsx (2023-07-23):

Assembly | Component Description | Signal | Component/Sensor Type | Manufacturer | MFG Part Number | Supplier | Supply Voltage |  |  |  | Current Draw |  |  |  | Signal Type |  | Signal Range |  | Measurement Range |  |  | Resolution | Operating Temperature |  |  | Price
 |  |  |  |  |  |  | Minimum | Nominal | Maximum | Units | Minimum | Nominal | Maximum | Units | A/D | Type | Minimum | Maximum | Minimum | Maximum | Units |  | Minimum | Maximum | Units
Reservoir
 | Reservoir pump | RsvrPmpAct | Fixed displacement pump
 | Flow Sensor | RsvrFlow | Flow sensor | Atlas Scientific | SEN-206F | Atlas Scientific | 3.0 |  | 24.0 | VDC | 8.0 |  | 25.0 | mA | Digital | Pulse counter |  |  | 0.2 (0.76) | 2.0 (7.6) | GPM (L/min) | ±2% | -20 | 80 | °C | $99.99
 | Temperature sensor 1 | RsvrTempIn | Waterproof Temperature Sensor | Maxim | DS18B20 | DFRobot | 3.0 |  | 5.5 | VDC |  |  |  |  | Digital | 9 to 12 bit |  |  | -55 | 125 | °C | ±0.5°C (-10°C to +85°C)
 | Temperature sensor 2 | RsvrTempOut | Waterproof Temperature Sensor | Maxim | DS18B20 | DFRobot | 3.0 |  | 5.5 | VDC |  |  |  |  | Digital | 9 to 12 bit |  |  | -55 | 125 | °C | ±0.5°C (-10°C to +85°C)
 | Water heater | RsvrHeaterAct
 | Water level sensor 1 | RsvrLvlMax | Liquid Level Switch | SST | LLC200D3SH-LLPK1 | Adafruit | 4.5 |  | 15.4 | VDC |  |  |  | mA | Digital |  |  |  |  |  |  |  | -25 | 80 | °C
 | Water level sensor 2 | RsvrLvlMed | Liquid Level Switch | SST | LLC200D3SH-LLPK1 | Adafruit | 4.5 |  | 15.4 | VDC |  |  |  | mA | Digital |  |  |  |  |  |  |  | -25 | 80 | °C
 | Water level sensor 3 | RsvrLvlMin | Liquid Level Switch | SST | LLC200D3SH-LLPK1 | Adafruit | 4.5 |  | 15.4 | VDC |  |  |  | mA | Digital |  |  |  |  |  |  |  | -25 | 80 | °C
Nutrient Control System
 | Nutrient control system pump | NCSPmpAct | Fixed displacement pump
 | TDS sensor | TDS | TDS Sensor
 | pH sensor | Ph | pH Sensor
 | pH increase pump | PhIncrPerPmp | Peristalic Pump | Atlas Scientific | EZO-PMP | Atlas Scientific | 12 (motor) 3.3 (logic) |  | 24 (motor) 5 (logic) | VDC |  |  |  |  | Digital | UART or I2C |  |  | 0.5 | 105 | mL/min | ±1%
 | pH decrease pump | PhDecrPerPmp | Peristalic Pump | Atlas Scientific | EZO-PMP | Atlas Scientific | 12 (motor) 3.3 (logic) |  | 24 (motor) 5 (logic) | VDC |  |  |  |  | Digital | UART or I2C |  |  | 0.5 | 105 | mL/min | ±1%
 | Nutrient_1 pump | Nutr1PerPmp | Peristalic Pump | Atlas Scientific | EZO-PMP | Atlas Scientific | 12 (motor) 3.3 (logic) |  | 24 (motor) 5 (logic) | VDC |  |  |  |  | Digital | UART or I2C |  |  | 0.5 | 105 | mL/min | ±1%
 | Nutrient_2 pump | Nutr2PerPmp | Peristalic Pump | Atlas Scientific | EZO-PMP | Atlas Scientific | 12 (motor) 3.3 (logic) |  | 24 (motor) 5 (logic) | VDC |  |  |  |  | Digital | UART or I2C |  |  | 0.5 | 105 | mL/min | ±1%
 | Nutrient_3 pump | Nutr3PerPmp | Peristalic Pump | Atlas Scientific | EZO-PMP | Atlas Scientific | 12 (motor) 3.3 (logic) |  | 24 (motor) 5 (logic) | VDC |  |  |  |  | Digital | UART or I2C |  |  | 0.5 | 105 | mL/min | ±1%
 | pH increase level sensor | PhIncrLvlMin | Liquid Level Switch | SST | LLC200D3SH-LLPK1 | Adafruit | 4.5 |  | 15.4 | VDC |  |  |  |  | Digital
 | pH decrease level sensor | PhDecrLvlMin | Liquid Level Switch | SST | LLC200D3SH-LLPK1 | Adafruit | 4.5 |  | 15.4 | VDC |  |  |  |  | Digital
 | Nutrient_1 level sensor | Nutr1LvlMin | Liquid Level Switch | SST | LLC200D3SH-LLPK1 | Adafruit | 4.5 |  | 15.4 | VDC |  |  |  |  | Digital
 | Nutrient_2 level sensor | Nutr2LvlMin | Liquid Level Switch | SST | LLC200D3SH-LLPK1 | Adafruit | 4.5 |  | 15.4 | VDC |  |  |  |  | Digital
 | Nutrient_3 level sensor | Nutr3LvlMin | Liquid Level Switch | SST | LLC200D3SH-LLPK1 | Adafruit | 4.5 |  | 15.4 | VDC |  |  |  |  | Digital
 | Feedback temperature sensor | NCSTempIn | Waterproof Temperature Sensor | Maxim | DS18B20 | DFRobot | 3.0 |  | 5.5 | VDC |  |  |  |  | Digital | 9 to 12 bit |  |  | -55 | 125 | °C | ±0.5°C (-10°C to +85°C)
 | Feedback flow sensor | NCSFlow | Liquid Flow Meter | Atlas Scientific | SEN-206F | Atlas Scientific | 3.0 |  | 24.0 | VDC | 8.0 |  | 25.0 | mA | Digital | Pulse counter |  |  | 0.2 (0.76) | 2.0 (7.6) | GPM (L/min) | ±2% | -20 | 80 | °C
Grow Area
 | LED grow lights | LEDCh1 | Grow light | Litever |  | Amazon |  | 12.0 |  | VDC |  | 4.0 |  | A
 | LED grow lights | LEDCh2 | Grow light | Litever |  | Amazon
 | LED grow lights | LEDCh3 | Grow light | Litever |  | Amazon
 | LED grow lights | LEDCh4 | Grow light | Litever |  | Amazon
 | Ambient light sensor | AmbLit | Ambient light sensor
 | Ambient environment sensor | AmbEnv | Temperature/Humidity/Pressure Sensor | Bosch | BME280 | Sparkfun | 3.3 |  | 5.0 | VDC | 0.005 |  | 1.0 | mA | Digital | SPI or I2C |  |  |  |  | -40°C - 85°C 0 - 100% RH 300 - 1100 hPa | 0.1°C (+-0.5°C deviation) 0.1% RH (+-2% RH deviation) |  | -40°C - 85°C | °C | $19.95 | https://www.sparkfun.com/products/13676
Control Enclosure
 | Main Controller |  | Control module
 | Main power switch |  | Power Switch
 | E-Stop |  | Emergency stop
 | Power distribution board |  | Nutrient Control board
 | Power supply |  | Power supply

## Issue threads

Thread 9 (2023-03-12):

TODO List - Schematic

joshlendi, 2023-03-12:

joshlendi, 2024-08-25:
Not going to include RTC circuit for minimum viable product. May consider adding this later in project.

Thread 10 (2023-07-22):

Review Power Management Subsystem

joshlendi, 2023-07-22:
Since we are using the Arduino Due directly on the board, we can take advantage of that boards voltage regulators.

Would like to simplify the different voltage levels available to only have one. 3.3V seems like the obvious one since it is what the Due uses

Review what voltage regulators are needed
What voltages should be available on the board?

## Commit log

2023-03-11 Created KiCAD 7.0 project
    Created blank KiCAD project to begin copying over design from previous KiCAD version. Added Libraries folder for storing project symbols and footprints
    [Dionysus-Power Distribution Board.kicad_pcb, Dionysus-Power Distribution Board.kicad_sch]
2023-03-12 Copied circuits from previous schematic
    Copied over the PMC, PWM, System Sensor, and GPIO pages from previous schematic
    [Dionysus-Power Distribution Board.kicad_sch, GPIO.kicad_sch, Power Management Controller.kicad_sch.kicad_sch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]
2023-04-09 Added Libraries and Copied previous work
    [Dionysus-Power Distribution Board.kicad_sch, GPIO.kicad_sch, Power Management Controller.kicad_sch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]
2023-04-17 Create Dionysus-Power Distribution Board-2023-04-15_112325.zip
2023-06-04 Updated Symbols and Redefined Hierarchical Pins
    Updated high side driver symbols, and added hierarchical pins to page 1
    [Dionysus-Power Distribution Board.kicad_sch, Power Management Controller.kicad_sch, Pulse Width Modulation Controller.kicad_sch]
2023-07-23 Added working copy of functional requirements docs
    [BoardCalculation.xlsx, Component Comparison.xlsx, Component Technical Information.xlsx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]
2023-07-23 Cleaned up functional requirements folder
    Cleaned up functional requirements folder.
    Began modifying functional requirements for using Arduino Due board as piggy back board
    [Dionysus Component Selection.xlsx, Dionysus Control System Component Selection.xlsx, IO Sheet.xlsx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]
2023-08-06 Creating power management controller tables
    Cleaned up spreadsheet to calculate power requirements for each voltage supply needed on power distribution board
    [Power Distribution Board Component Calculator.xlsx]
2023-08-06 Started IO sheet and finished calculator spreadsheet
    Started an IO sheet for all signals on PDB. Need to assign IO to Arduino and add various power and ground signals for terminal blocks.
    [IO Sheet.xlsx, Power Distribution Board Component Calculator.xlsx, Power Distribution Board Component Selection.xlsx]
2023-08-13 Continued work on IO sheet
    [IO Sheet.xlsx]
2023-08-13 Continued IO sheet and revised PMC figure
    Assigned remaining Arduino Due IO on controller IO sheet. Revised PMC figure for functional requirements for updated power management.
    Continue working on IO sheet and subsystem figures for functional requirements. Need to create terminal block layout diagram for TB numbering
    [IO Sheet.xlsx]
2023-08-15 Consolidated IO sheets
    Combined board IO and controller IO sheets. Going to use 1 IO sheet moving forward. First part of IO sheet will be board IO. Second part is internal microcontroller IO
    [IO Sheet.xlsx, Power Distribution Board Component Calculator.xlsx]
2023-08-16 Continued on combined IO sheet
    [IO Sheet.xlsx]
